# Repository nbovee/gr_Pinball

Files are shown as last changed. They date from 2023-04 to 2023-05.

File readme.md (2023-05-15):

# Graduate Embedded Project Proposal: Pinball

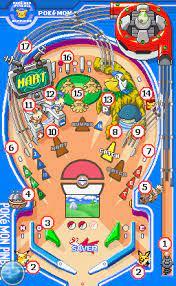
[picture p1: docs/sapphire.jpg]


This repository contains a project for the design and build of a half-scale pinball table. Modern pinball tables use 48V systems with 27mm steel balls. We will reduce our power to 24V for easier sourcing of components, and reduce the size of the steel ball to 19mm (~½ mass of the standard) to maintain the best approximation of game feel. The approximate layout will match the screenshot on the right of Pokemon Pinball : Sapphire’s table, but may not remain Pokemon themed. To reduce overall complexity, features 2, 4, 5,  8, & 10-13 are intended to be removed.

Mechanical design components will be largely laser cut frames, with acrylic and 3D printed parts as necessary for cosmetic and detail work as needed. Solenoid assemblies require some mechanical level design and may be waterjet aluminum to eliminate potential issues in the timescale of this project. A poster print may be requested to serve as the art for the pinball board. AC and 24V components added by Nick will be soldered and covered for safety.
While individual sensors may be considered trivial, the greater embedded programming challenge is in the implementation of a large state machine with numerous inputs and feedback methods. Unless time cost is trivial, all components active during gamestate must be non blocking to ensure high speed play is responsive. To accomplish this, we are best off using interrupts, an event system, or a scheduler. We selected a scheduler to ensure constant polling of solenoids to avoid burnout.

## Details

### Implemented Components

| Name | Components | Implemented | Notes |
| --- | --- | --- | --- |
| Flipper Assembly | Solenoid, PWM, FET | Yes | Safe_Solenoid class to avoid burnout |
| Pop Bumper Assembly | Solenoid, PWM, FET | Yes | ASM design extremely challenging |
| Arcade Buttons | 2x 30mm 1x 24mm Sanwa OBSN | Yes | |
| Ball Detection | Hall Effect sensors | Not Yet | Not practical to have on i2c, Low/High on digital |
| Screen | i2c LCD | Not Yet | Library |
| Tilt Detection | IMU | Not Yet | Library |
| Scheduler | Software Only | Yes | Reduces energy usage and simplifies main.cpp |

### Removed Components

| Name | Components | Justification |
| --- | --- | --- |
| Name Input | Hex Keypad | Limited affect on total design |
| Slingshot Assembly | Solenoid, FET, Prox Switch | Extraneous mechanical design |
| Lights | Addressable LED | Time constraint, simple implementation |
| Sounds | Speakers, SD reader and playback IC | Couldn't find licensable pokemon sfx library |

### C4 Context Diagram

```mermaid
C4Context
UpdateLayoutConfig("3","10")
title Pinball System
  
Deployment_Node(pball2, "Control Logic"){
    ContainerDb(state1, "Last State", "I/O, Flags, Score")
    ContainerDb(state2, "Current IO State", "I/O, Flags, Score")
    ComponentQueue(sch1, "Looping Task Handler", "Scheduler")
}

Boundary(tasks, "Tasks", "Tasks"){
    Component(t6, "Game Step", "Task", "Collects input states, processes game rules.")
    Component(t1, "Flippers", "Task")
    Component(t2, "Bumpers", "Task")
    Component(t3, "GPIO", "Task(s)")
    Component(t4, "LCD", "Task")
    Component(t5, "IMU", "Task")
}

Boundary(components, "I/O Components", "Various Objects"){
    Component(safe_solenoid, "Switched Solenoid", "Safe_Solenoid", "Handler for flippers & popbumpers.")
    Component(startbut, "Start Button", "GPIO")
    Component(hall, "Ball Sensors", "GPIO")
    Component(lcd, "LCD")
    Component(imu, "Tilt Detect", "IMU")
}

Boundary(pcomponents, "External", "Various Objects"){
    Person_Ext(player,"Pinball Enjoyer")
    Component_Ext(launcher, "Ball Launcher")
    Component_Ext(ball, "Steel Ball")
}

Rel(sch1, t1, "")
Rel(sch1, t2, "")
Rel(sch1, t3, "")
Rel(sch1, t4, "")
Rel(sch1, t5, "")
Rel(sch1, t6, "")

%%Rel(t1, state2, "")
%%Rel(t2, state2, "")
%%Rel(t3, state2, "")
%%Rel(t5, state2, "")

Rel(player, startbut, " ")
Rel(player, safe_solenoid, " ")
Rel(ball, hall, "")
Rel(player, launcher, "")
Rel(launcher, ball, "")
Rel(player, imu, "")

%% object to tasks
BiRel(safe_solenoid, t1, "")
BiRel(safe_solenoid, t2, "")
Rel(startbut, t3, "")
Rel(hall, t3, "")
Rel(lcd, t4, "")
Rel(imu, t5, " ")

BiRel(t6, state1, "")
BiRel(t6, state2, "")
BiRel(safe_solenoid, ball, "")
Rel(lcd, player, "")

Rel(sch1, t1, " ")
```

### External Libraries

| Name | License | Notes |
| --- | --- | --- |
| SPI | LGPL 2.1 | AVR Core library |
| TaskScheduler | BSD-3-Clause | |
| Liquid_Crystal_i2c | LGPL 2.1* | None listed, but derived from LGPL 2.1 so must inherit |
| Adafruit_MPU6050 | BSD-3-Clause | |
| Adafruit BusIO | MIT | |
| Adafruit Unified Sensor | MIT | |

## Challenges, Fixes, Future Work
 
Currently the selected MOSFETs do not function as expected. Under full PWM they only provide 20% of the expected power to the solenoids for flippers and popbumpers, and due to this they do not actuate. Different FETs must be selected for full function.

Future work will include LED and Sound function, as well as improvements to the game board and interactable components. 

## Team: Qualifications & Eval

Nick is an experienced engineer and computer scientist with a large background in robotics and electromechanical design. His work in Engineering in the creation of similar equipment and guiding student embedded design projects, is highly relevant, and he has work experience with industrial and home robotics. As a student he retrofit a drive by wire systems into a golf cart for undergraduate senior design, and is currently performing research in robotics and AI with Dr. Ho. Recent personal projects include custom fighting game controllers, keyboards, and an MTG card sorting machine.

Nick was responsible for the entirety of the project. With these skills Nick has done well with the project and has ensured code is easily modifiable to allow cut components to be reintroduced as needed. Between unfortunate personal circumstances and full-time responsibilities more features than desired were cut before final delivery.

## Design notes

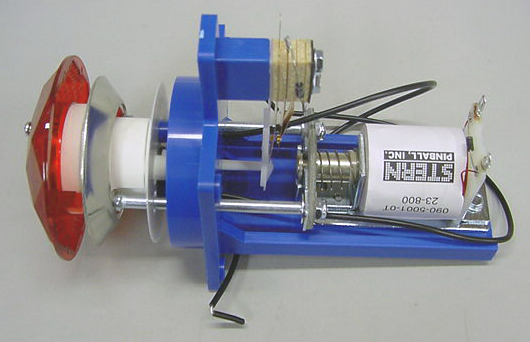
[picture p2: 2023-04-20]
MCAD/popb-0010.png

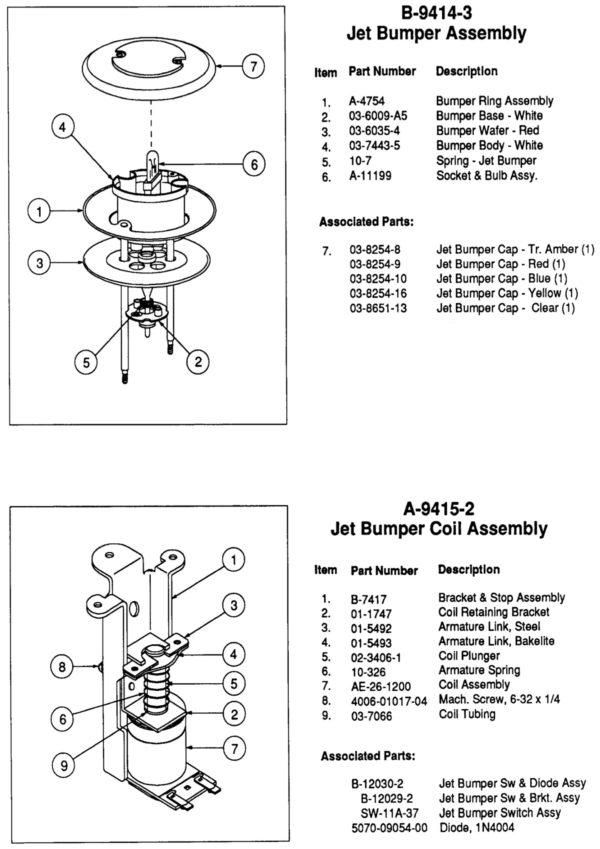
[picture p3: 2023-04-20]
MCAD/Screen-Shot-2020-10-26-at-5.49.52-PM-e1603934165629.jpg

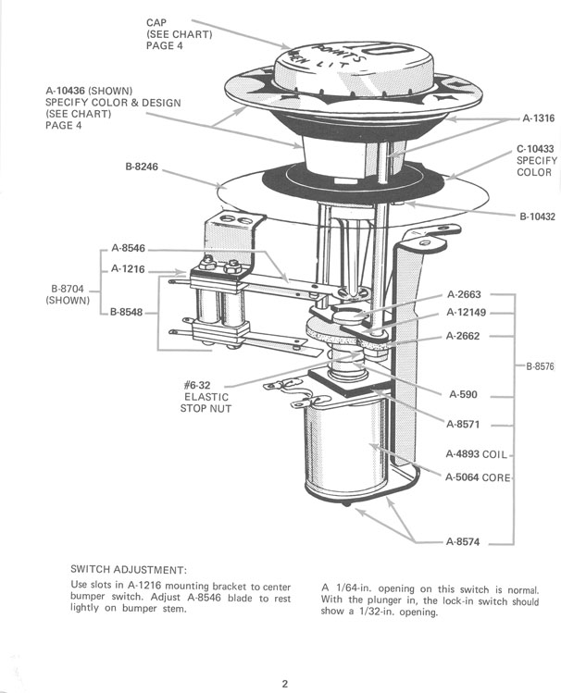
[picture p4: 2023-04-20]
MCAD/gtb_76_cat_p2.jpg

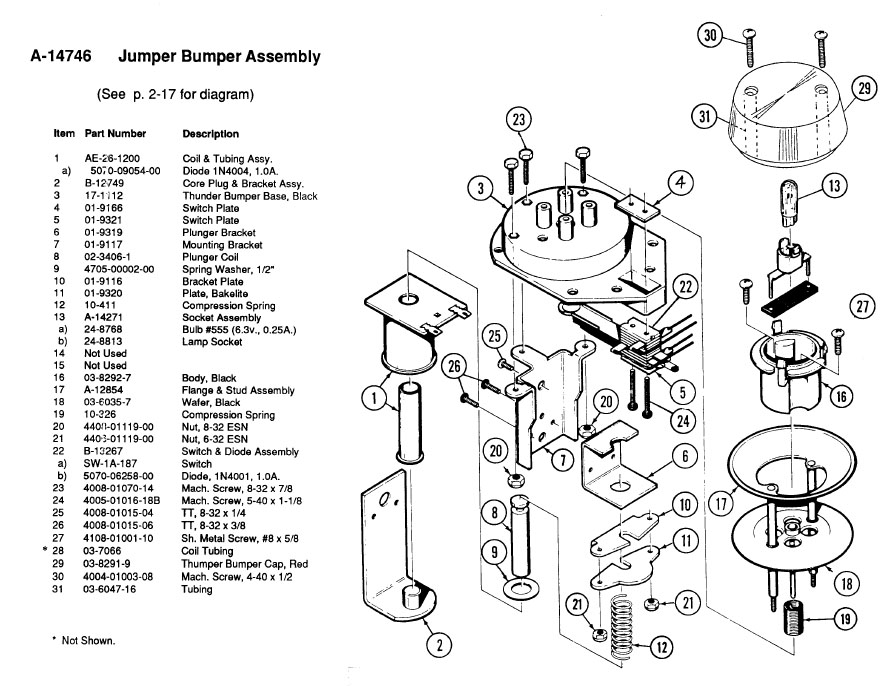
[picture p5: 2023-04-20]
MCAD/a-14746.jpg

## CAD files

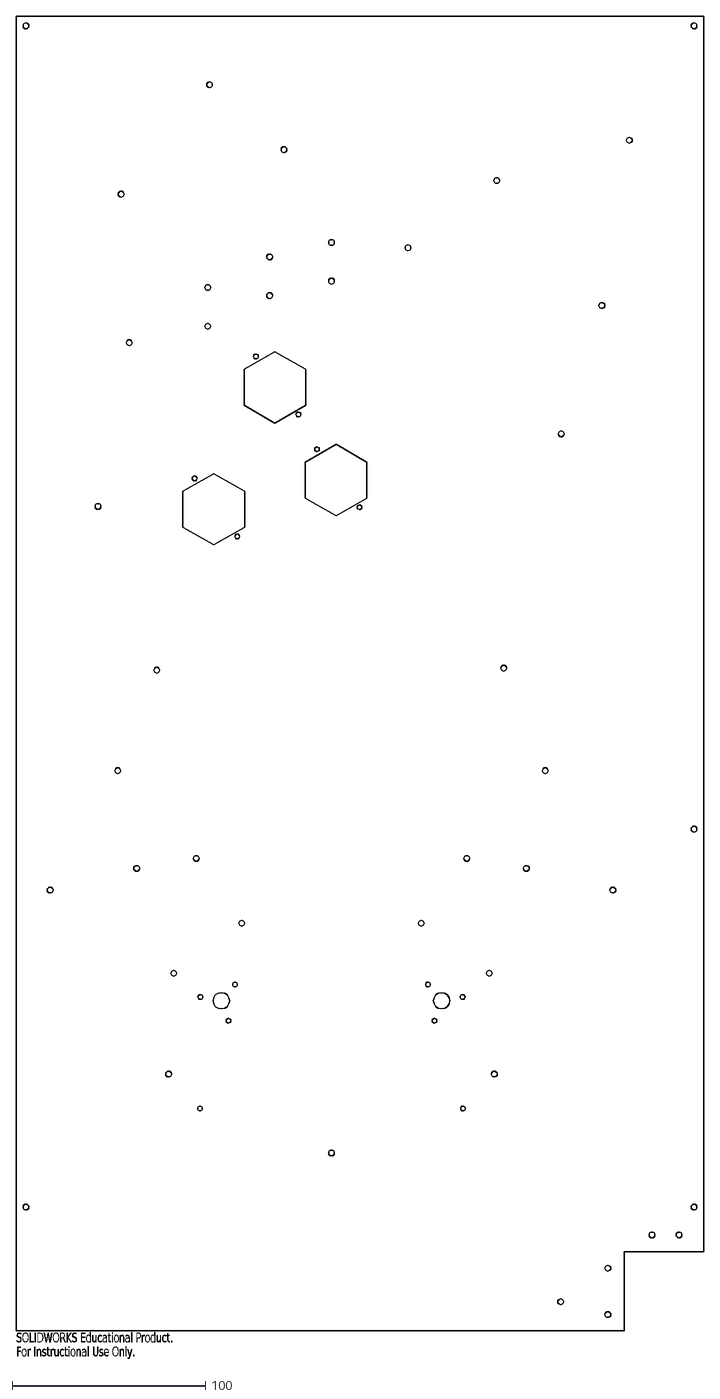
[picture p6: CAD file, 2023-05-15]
MCAD/Export/Field_Base.DXF
SOLIDWORKS Educational Product.
For Instructional Use Only.

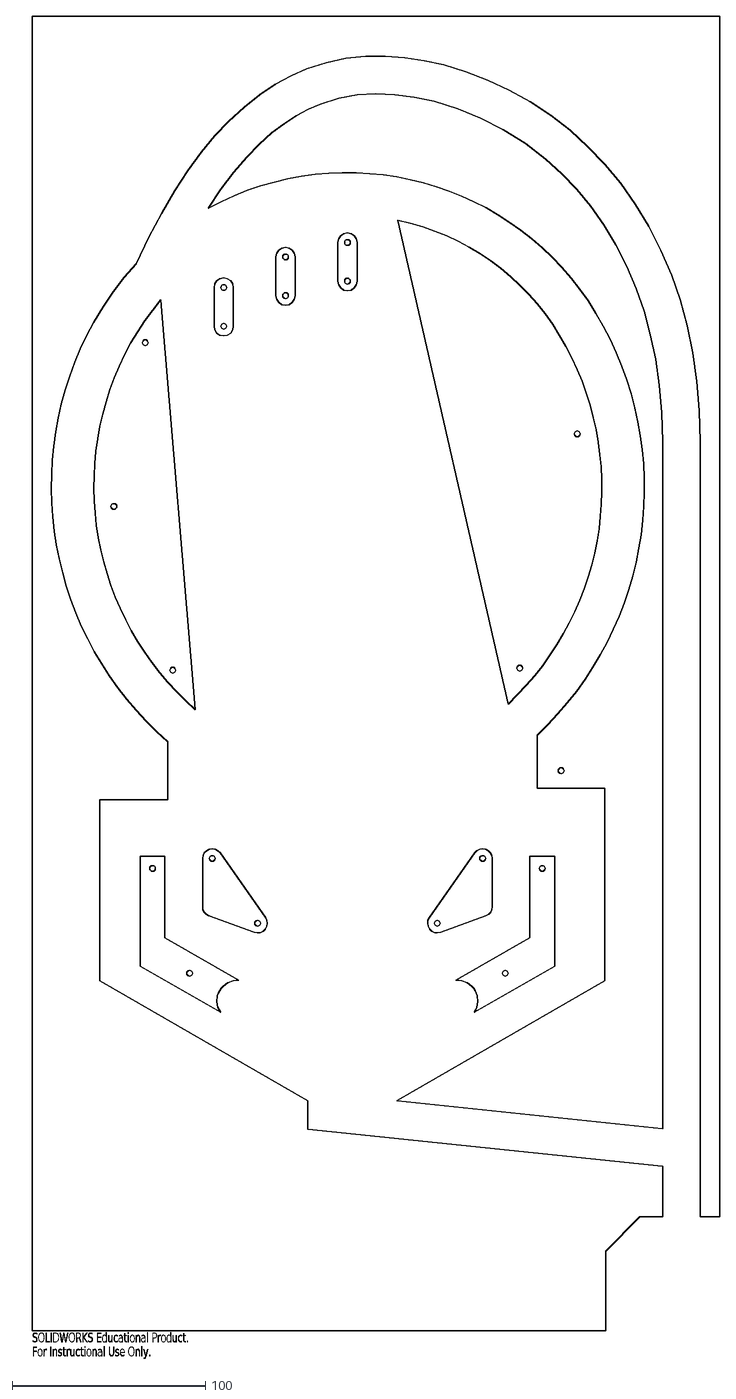
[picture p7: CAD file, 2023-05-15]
MCAD/Export/Field_Frame.DXF
SOLIDWORKS Educational Product.
For Instructional Use Only.

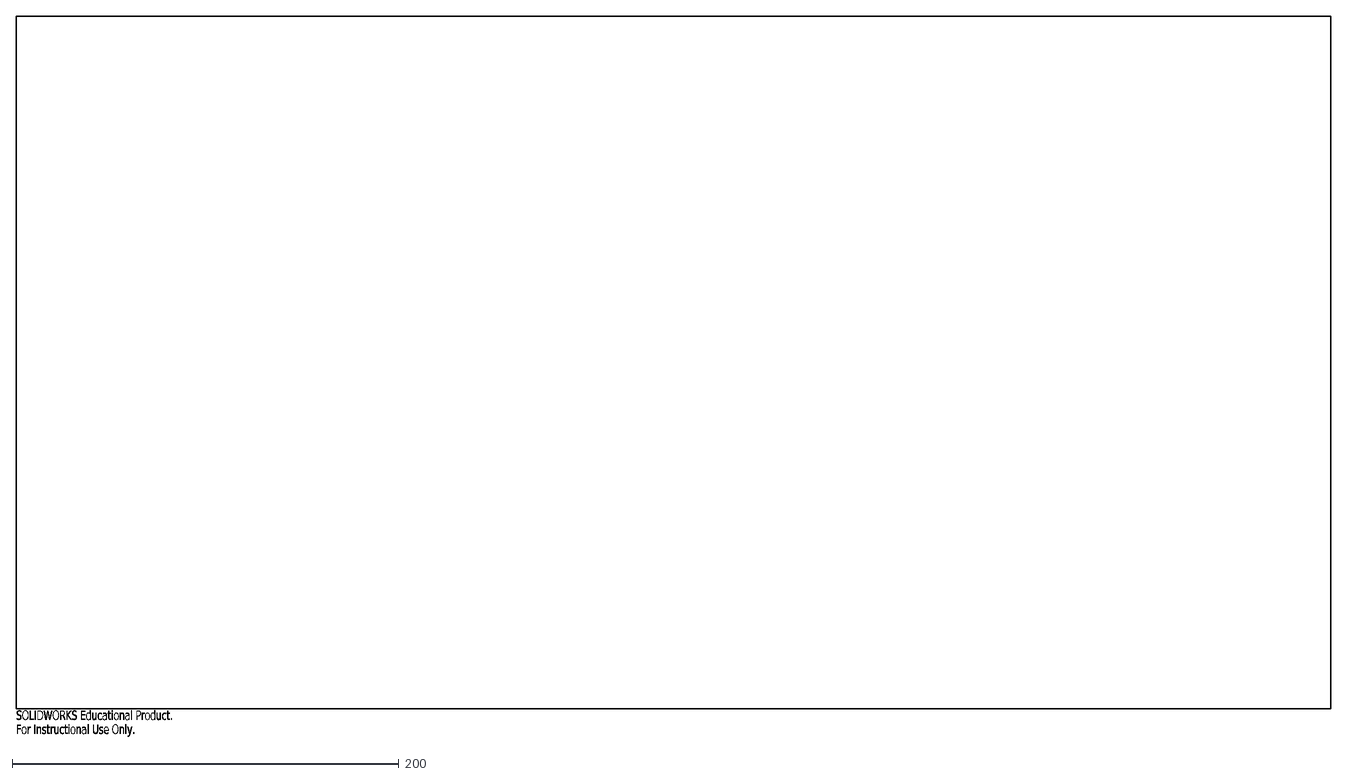
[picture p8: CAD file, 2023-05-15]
MCAD/Export/Base.DXF
SOLIDWORKS Educational Product.
For Instructional Use Only.

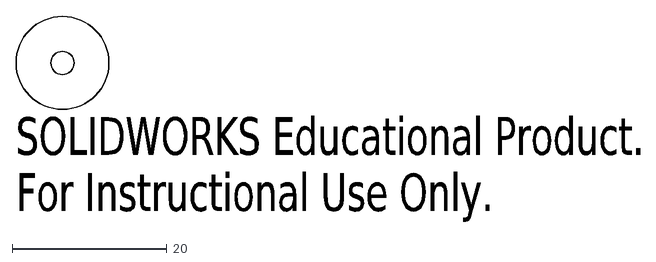
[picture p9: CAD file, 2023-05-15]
MCAD/Export/SmallRest.DXF
SOLIDWORKS Educational Product.
For Instructional Use Only.

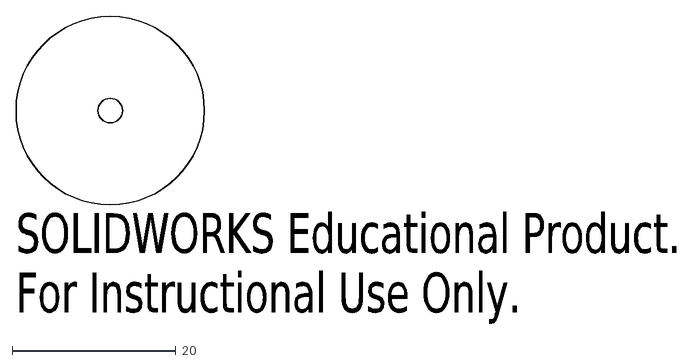
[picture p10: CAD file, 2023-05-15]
MCAD/Export/LargeRest.DXF
SOLIDWORKS Educational Product.
For Instructional Use Only.

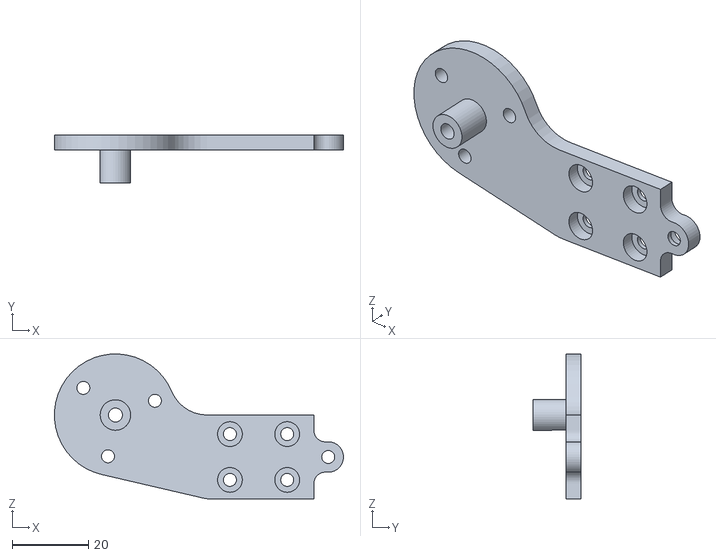
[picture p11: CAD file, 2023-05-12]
MCAD/Export/Flipper_Plate.STL
75.7 x 12.6 x 38.0

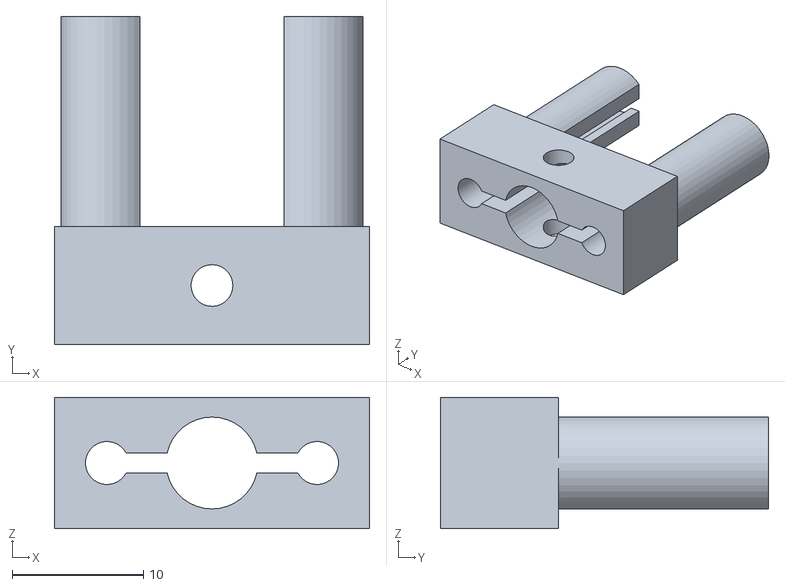
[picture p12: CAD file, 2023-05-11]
MCAD/Export/PopBumper_RodCoupler.STL
24.0 x 25.0 x 10.0

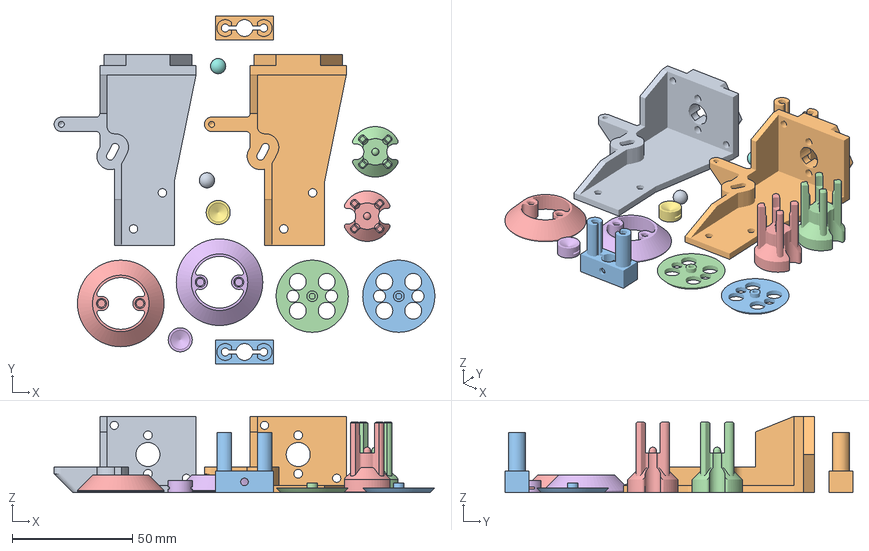
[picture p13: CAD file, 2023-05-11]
MCAD/Export/PopBumper_SwitchBall.3mf
158.3 x 144.7 x 31.8 mm
PopBumper_SwitchBall.STL x 2
PopBumper_Bracket.STL x 2
PopBumper_RodCoupler.STL x 2
PopBumper_Skirt.STL x 2
PopBumper_Cap.STL x 2
PopBumper_UpperRing.STL x 2
PopBumper_Cup.STL x 2

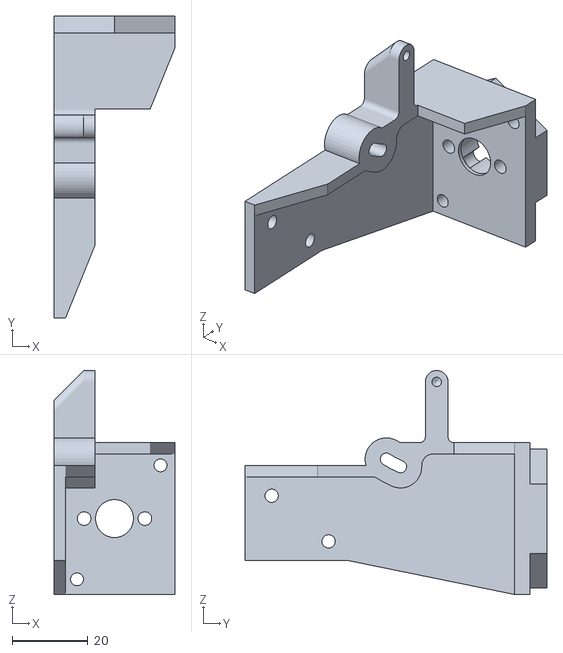
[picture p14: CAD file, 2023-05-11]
MCAD/Export/PopBumper_Bracket.STL
31.8 x 79.5 x 59.0

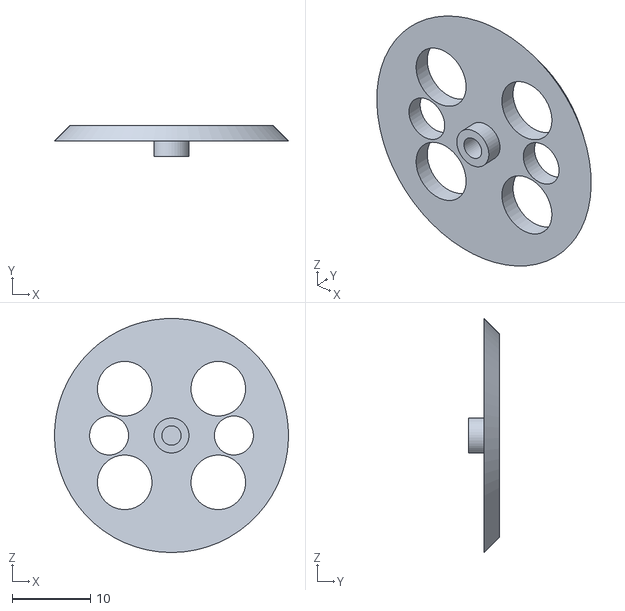
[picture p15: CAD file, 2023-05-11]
MCAD/Export/PopBumper_Skirt.STL
30.0 x 4.00 x 30.0

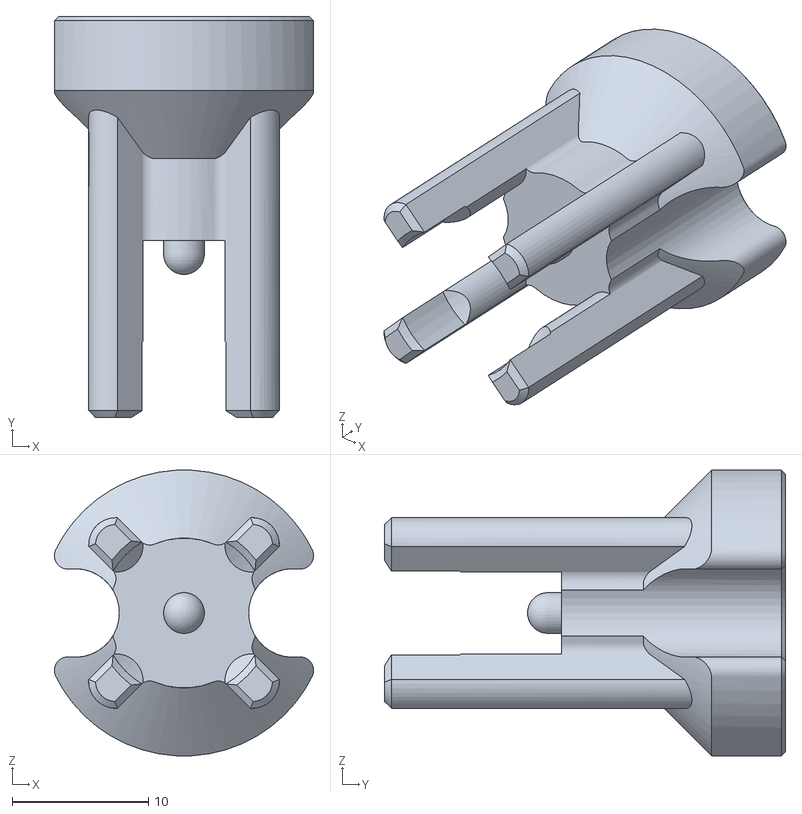
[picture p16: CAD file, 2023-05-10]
MCAD/Export/PopBumper_Cap.STL
19.0 x 29.4 x 21.0

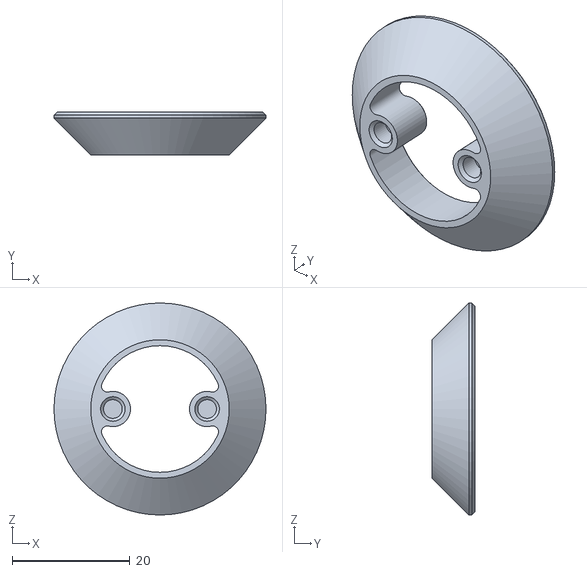
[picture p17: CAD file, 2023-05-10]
MCAD/Export/PopBumper_UpperRing.STL
36.0 x 7.25 x 36.0

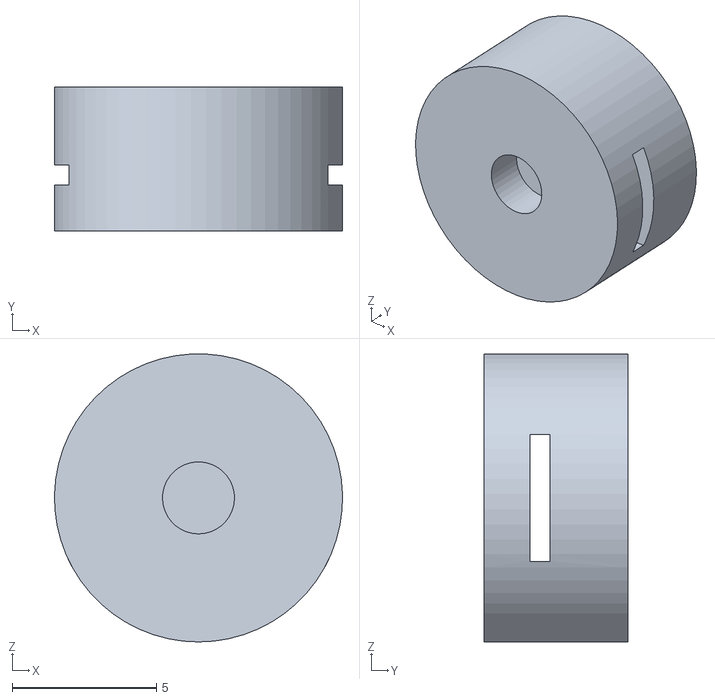
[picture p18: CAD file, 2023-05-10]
MCAD/Export/PopBumper_Cup.STL
10.00 x 5.00 x 9.99

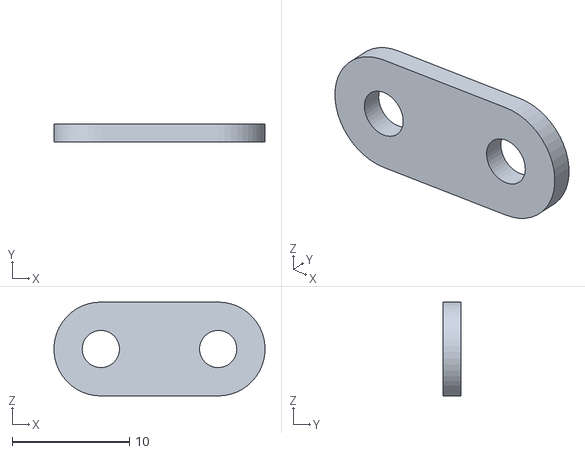
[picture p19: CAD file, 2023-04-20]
MCAD/Export/Flipper_Coupler.STL
18.0 x 1.50 x 8.00

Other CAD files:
MCAD/Export/Flipper_Lever.3mf
MCAD/Export/FrameJoint.STL
MCAD/Export/PopBumper_Skirt_Test.STL
MCAD/Export/TestPart.DXF
MCAD/Export/Back_Side.DXF
MCAD/Export/Flipper.STL
MCAD/Export/Flipper_Lever.STL
MCAD/Export/Flipper_Support.STL
MCAD/Export/Flippers.3mf
MCAD/Export/Front_Side.DXF
MCAD/Export/PopBumper_SwitchBall.STL
MCAD/Export/Right_Side.DXF
MCAD/Export/Shooter_Bracket.STL

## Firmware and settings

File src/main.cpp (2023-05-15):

// required since we are in PlatformIO, not Arduino IDE
#include <Arduino.h>

// defines kept here to avoid clutter
#include <IOdef.h>

// external
#include <TaskScheduler.h>
#include <LiquidCrystal_I2C.h>
#include <Adafruit_MPU6050.h>
#include <Adafruit_Sensor.h>

// internal
#include <Safe_Solenoid.h>

// Scheduler allows for microsleeps to save energy, and avoids messy logic for us.
Scheduler r;

// Checks acceleration to look for cheaters.
Adafruit_MPU6050 imu = Adafruit_MPU6050();

// Displays score.
LiquidCrystal_I2C lcd = LiquidCrystal_I2C(0x27, 16, 2);

long score;
bool cheat_flag;
bool end_flag;

// Game Objects
Safe_Solenoid l_flipper = Safe_Solenoid(LBMP_b, LBMP_s, FLIPPER_EOT_PWM);
Safe_Solenoid r_flipper = Safe_Solenoid(RBMP_b, RBMP_s, FLIPPER_EOT_PWM);
Safe_Solenoid pop_1 = Safe_Solenoid(POP1_b, POP1_s);
Safe_Solenoid pop_2 = Safe_Solenoid(POP2_b, POP2_s);
Safe_Solenoid pop_3 = Safe_Solenoid(POP3_b, POP3_s);

// void task wrappers
void flippers()
{
  Serial.print("T:Flippers");
  Serial.print(" ");
  Serial.print(l_flipper.step());
  Serial.print(" ");
  Serial.println(r_flipper.step());
}

void bumpers()
{
  Serial.println("T:Bumpers");
  Serial.print(pop_1.step());
  Serial.print(pop_2.step());
  Serial.println(pop_3.step());
  if (pop_1._input_state || pop_2._input_state || pop_3._input_state)
  { // bumper has been triggered somehow.
    score += 100;
  }
}

void hall_effects()
{
  Serial.println("T:Hall Effects");
  bool h1 = !digitalRead(HE1);
  bool h2 = !digitalRead(HE2);
  bool h3 = !digitalRead(HE3);
  // ball left playing area
  if (h1)
  {
    end_flag = true;
  }
  // ball entered or exit loop
  if (h2 || h3)
  {
    score += 500;
  }
}

void find_cheater()
{
  Serial.println("T:IMU");
  sensors_event_t a, g, temp;
  imu.getEvent(&a, &g, &temp);
  float xy_accel = sqrt(a.acceleration.x * a.acceleration.x + a.acceleration.y * a.acceleration.y);
  float xyz_accel = sqrt(xy_accel * xy_accel + a.acceleration.z * a.acceleration.z);
  if (xyz_accel > GRAVITY * CHEAT_TOLERANCE)
  {
    cheat_flag = true;
  }
}

void show_score()
{
  Serial.println("T:LCD");
  lcd.clear();
  lcd.setCursor(0, 0);
  lcd.print(score);
}

void start()
{
  if (!digitalRead(START_b))
  {
    r.enableAll(true);
  }
}

// all disabled by default until the start input is received
Task flip(_TASK_INTERVAL, TASK_FOREVER, &flippers, &r, false);
Task bump(_TASK_INTERVAL, TASK_FOREVER, &bumpers, &r, false);
Task hall(_TASK_INTERVAL, TASK_FOREVER, &hall_effects, &r, false);
Task cheat_test(_TASK_INTERVAL, TASK_FOREVER, &find_cheater, &r, false);
Task lcd_disp(_TASK_INTERVAL, TASK_FOREVER, &show_score, &r, false);
// by being the only enabled task, nothing will run until this task enables everything.
Task starter(_TASK_INTERVAL, TASK_FOREVER, &start, &r, true);

/*
  Initializes the program
*/
void setup()
{
  // all tasks update at the same interval
  // we'll assume game logic is robust enough to not a need priority system
  Serial.begin(9600);
  l_flipper.begin();
  r_flipper.begin();
  imu.begin();
  lcd.init();
  lcd.backlight();
  lcd.print("Waiting for Start.");
  score = 0;
  pinMode(START_b, INPUT_PULLUP);
  pinMode(HE1, INPUT_PULLUP);
  pinMode(HE2, INPUT_PULLUP);
  pinMode(HE3, INPUT_PULLUP);
}

/*
  Iterates through the scheduler
*/
void loop()
{
  r.execute();
  if (cheat_flag)
  {
    lcd.setCursor(0, 0);
    lcd.print("Cheat detected!");
    exit(1);
  }
  if (end_flag)
  {
    exit(0);
  }
}

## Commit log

2019-11-26 Editing Driver
2019-11-26 AirportSystem creation, Driver updates
2019-12-01 Updated Driver, Wrapper Class, and selected List implementation
2019-12-02 Added methods for (de)queueing and peeking
2021-05-04 start of driver/service user
2021-05-04 working driver.py
2021-05-04 changed driver.py to price_check.py
2023-04-24 pull in data from coursework repo
    [Back_Side.DXF, Flipper.STL, Flipper_Coupler.STL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]
2023-05-10 pop bumper rework
    [PopBumper_Bracket.STL, PopBumper_Cap.STL, PopBumper_Cup.STL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]
2023-05-10 prog, incomplete rework to use scheduler
    [main.cpp]
2023-05-11 scheduling implemented for flipper
    [PopBumper_Bracket.STL, PopBumper_RodCoupler.STL, PopBumper_Skirt.STL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]
2023-05-12 abstract solenoid
2023-05-15 commit for grade
    [Base.DXF, Field_Base.DXF, Field_Frame.DXF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]
